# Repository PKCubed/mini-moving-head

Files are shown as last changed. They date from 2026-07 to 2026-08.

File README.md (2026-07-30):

# Mini Moving Head

This project aims to create a miniature moving head light fixture for my miniature stage. This fixture needs to have motorized pan and tilt, and should have a bright LED with a collimating lens to create as tight of a beam as possible. For now, a single color LED is acceptable due to the size constraints, as a multicolor LED with individual separate LED dies in side the package causes individual colored beams preventing color mixing.

This project consists of a custom circuit board with an RP2040 on board to take in unbalanced "DMX" signals from the "DMX" bus and read channel data for it's pan and tilt position and the brightness of it's LED. The circuit board drives two 9 gram servos with PWM to give pan and tilt and a constant current driver with PWM control for the LED. We'll need to make sure that the PWM is fast enough that it's not going to cause artifacts on cameras under any circumstances.



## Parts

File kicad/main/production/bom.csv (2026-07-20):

Designator | Footprint | Quantity | Value | LCSC Part #
C1, C2, C9 | C_0805 | 3 | 10uF | C15850
C10, C13 | C_0402 | 2 | 1uF | C52923
C11, C12, C3, C4, C5, C6 | C_0402 | 6 | 100nF | C1525
C15, C16 | C_0402 | 2 | 30pF | C1570
D2 | D_0603 | 1 | Red | C2286
D3 | D_0805 | 1 | Green | C2297
J1, J10, J7, J8 | 2-position | 4 | Conn_01x02
J2, J3 | 3-position | 2 | Conn_01x03
J4, J5 | PinHeader_1x02_P2.54mm_Vertical | 2 | Conn_01x02
J6 | TYPE-C-SMD_HX-TYPE-C-16PIN | 1 | Connector, USB-TYPE-C-16P | C2927039
L2 | IND-SMD_L3.5-W3.0 | 1 | 4.7uH
R1, R11 | R_0402 | 2 | 10kΩ | C25744
R10, R9 | R_1206 | 2 | 100mΩ | C25334
R2, R3 | R_0402 | 2 | 5.1kΩ | C25905
R4, R5 | R_0603 | 2 | 27Ω | C25190
R6 | R_0402 | 1 | 1kΩ | C11702
R7 | R_0402 | 1 | 510Ω | C25123
R8 | R_0603 | 1 | 430Ω | C23170
S1, S2 | SW_TS-1088-AR02016 | 2 | Tactile Button, 160gf | C720477
TP1 | TestPoint_Pad_D1.0mm | 1 | GPIO0
TP2 | TestPoint_Pad_D1.0mm | 1 | GPIO4
TP3 | TestPoint_Pad_D1.0mm | 1 | GPIO5
TP4 | TestPoint_Pad_D1.0mm | 1 | GPIO6
TP5 | TestPoint_Pad_D1.0mm | 1 | GPIO28
TP6 | TestPoint_Pad_D1.0mm | 1 | GPIO29
U2 | SOT-23-3_L2.9-W1.6-P1.90-LS2.8-BR | 1 | XC6206P332MR | C5446
U3 | SOIC-8_L5.3-W5.3-P1.27-LS8.0-BL | 1 | ~
U4 | SOT-23-5_L3.0-W1.7-P0.95-LS2.8-BR | 1 | ~
U5 | QFN-56-1EP_7x7mm_P0.4mm_EP3.2x3.2mm_ThermalVias | 1 | RP2040 | C2040
X1 | CRYSTAL-SMD_4P-L3.2-W2.5-BL | 1 | X322512MSB4SI | C9002

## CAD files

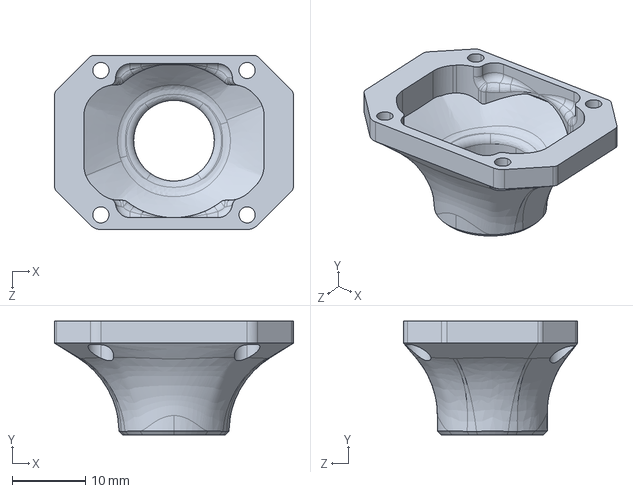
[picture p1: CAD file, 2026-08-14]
cad/Part7.STEP
32.6 x 15.5 x 23.8 mm

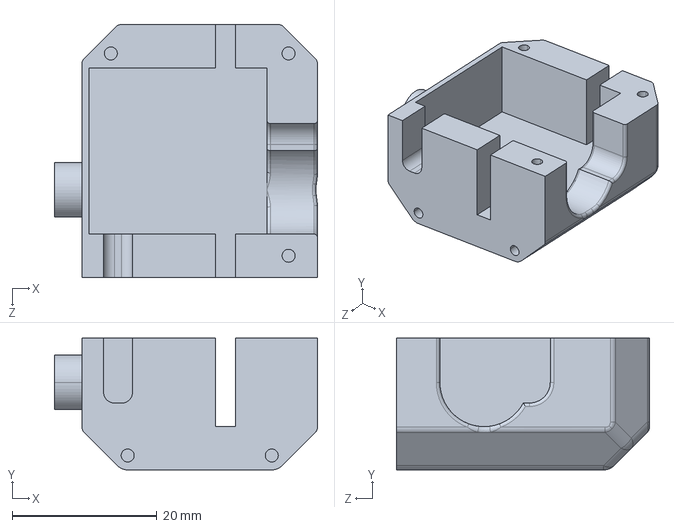
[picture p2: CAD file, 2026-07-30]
cad/Part4.STEP
36.4 x 18.2 x 35.0 mm

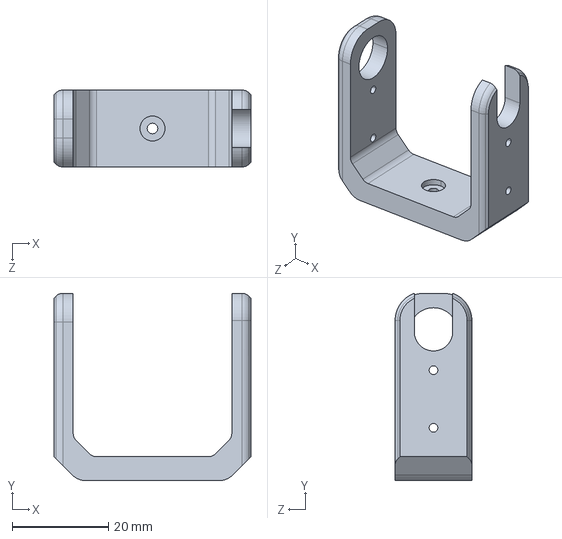
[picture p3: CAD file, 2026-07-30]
cad/Part2.STEP
41.0 x 39.0 x 16.0 mm

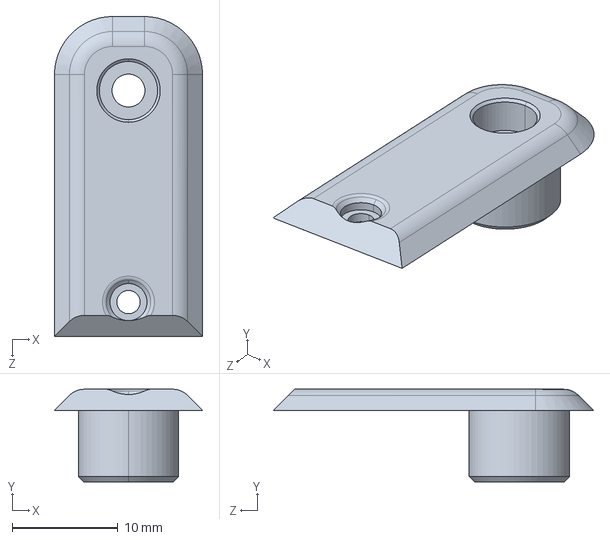
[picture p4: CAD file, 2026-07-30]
cad/Part3.STEP
14.0 x 8.75 x 30.2 mm

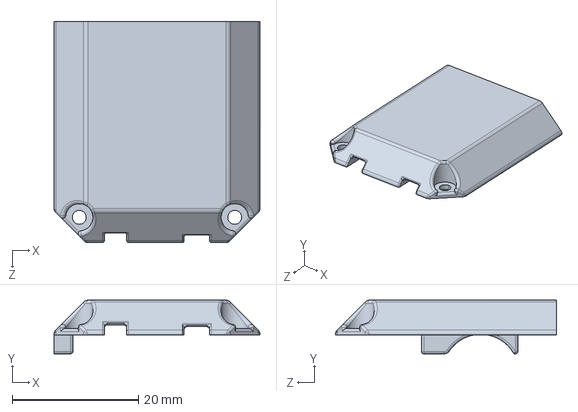
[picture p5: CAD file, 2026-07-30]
cad/Part5.STEP
32.6 x 8.50 x 35.0 mm

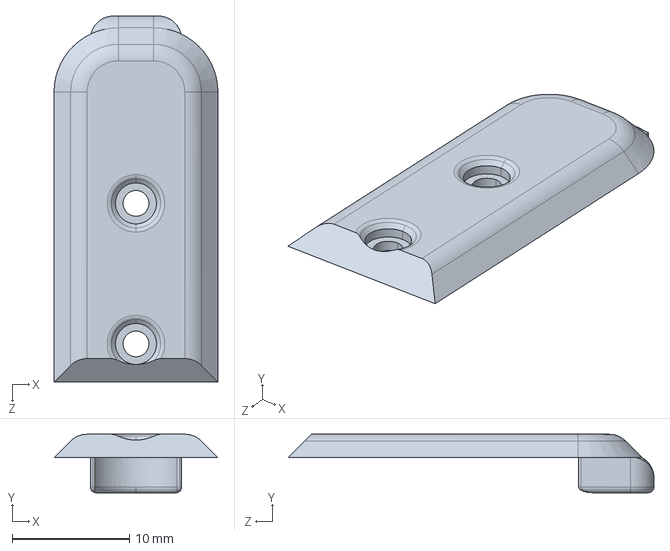
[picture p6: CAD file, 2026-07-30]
cad/Part6.STEP
14.0 x 5.00 x 31.2 mm

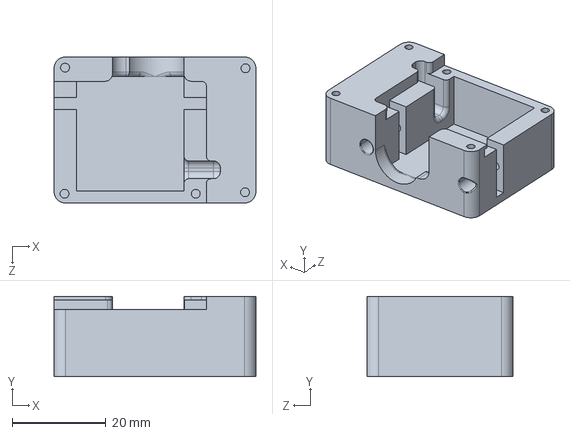
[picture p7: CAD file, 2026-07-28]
cad/Part1.STEP
43.1 x 17.1 x 31.2 mm

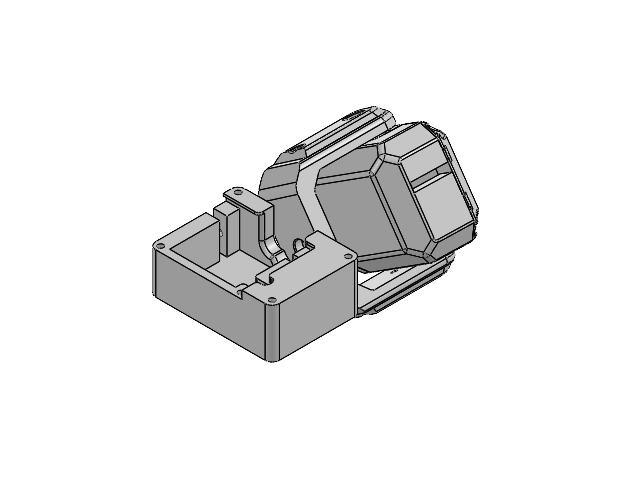
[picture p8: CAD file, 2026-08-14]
cad/Assem1.SLDASM


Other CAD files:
cad/Part1.3mf
cad/Part1.SLDPRT
cad/Part2.SLDPRT
cad/Part3.SLDPRT
cad/Part4.SLDPRT
cad/Part5.SLDPRT
cad/Part6.SLDPRT
cad/Part7.3MF
cad/Part7.SLDPRT

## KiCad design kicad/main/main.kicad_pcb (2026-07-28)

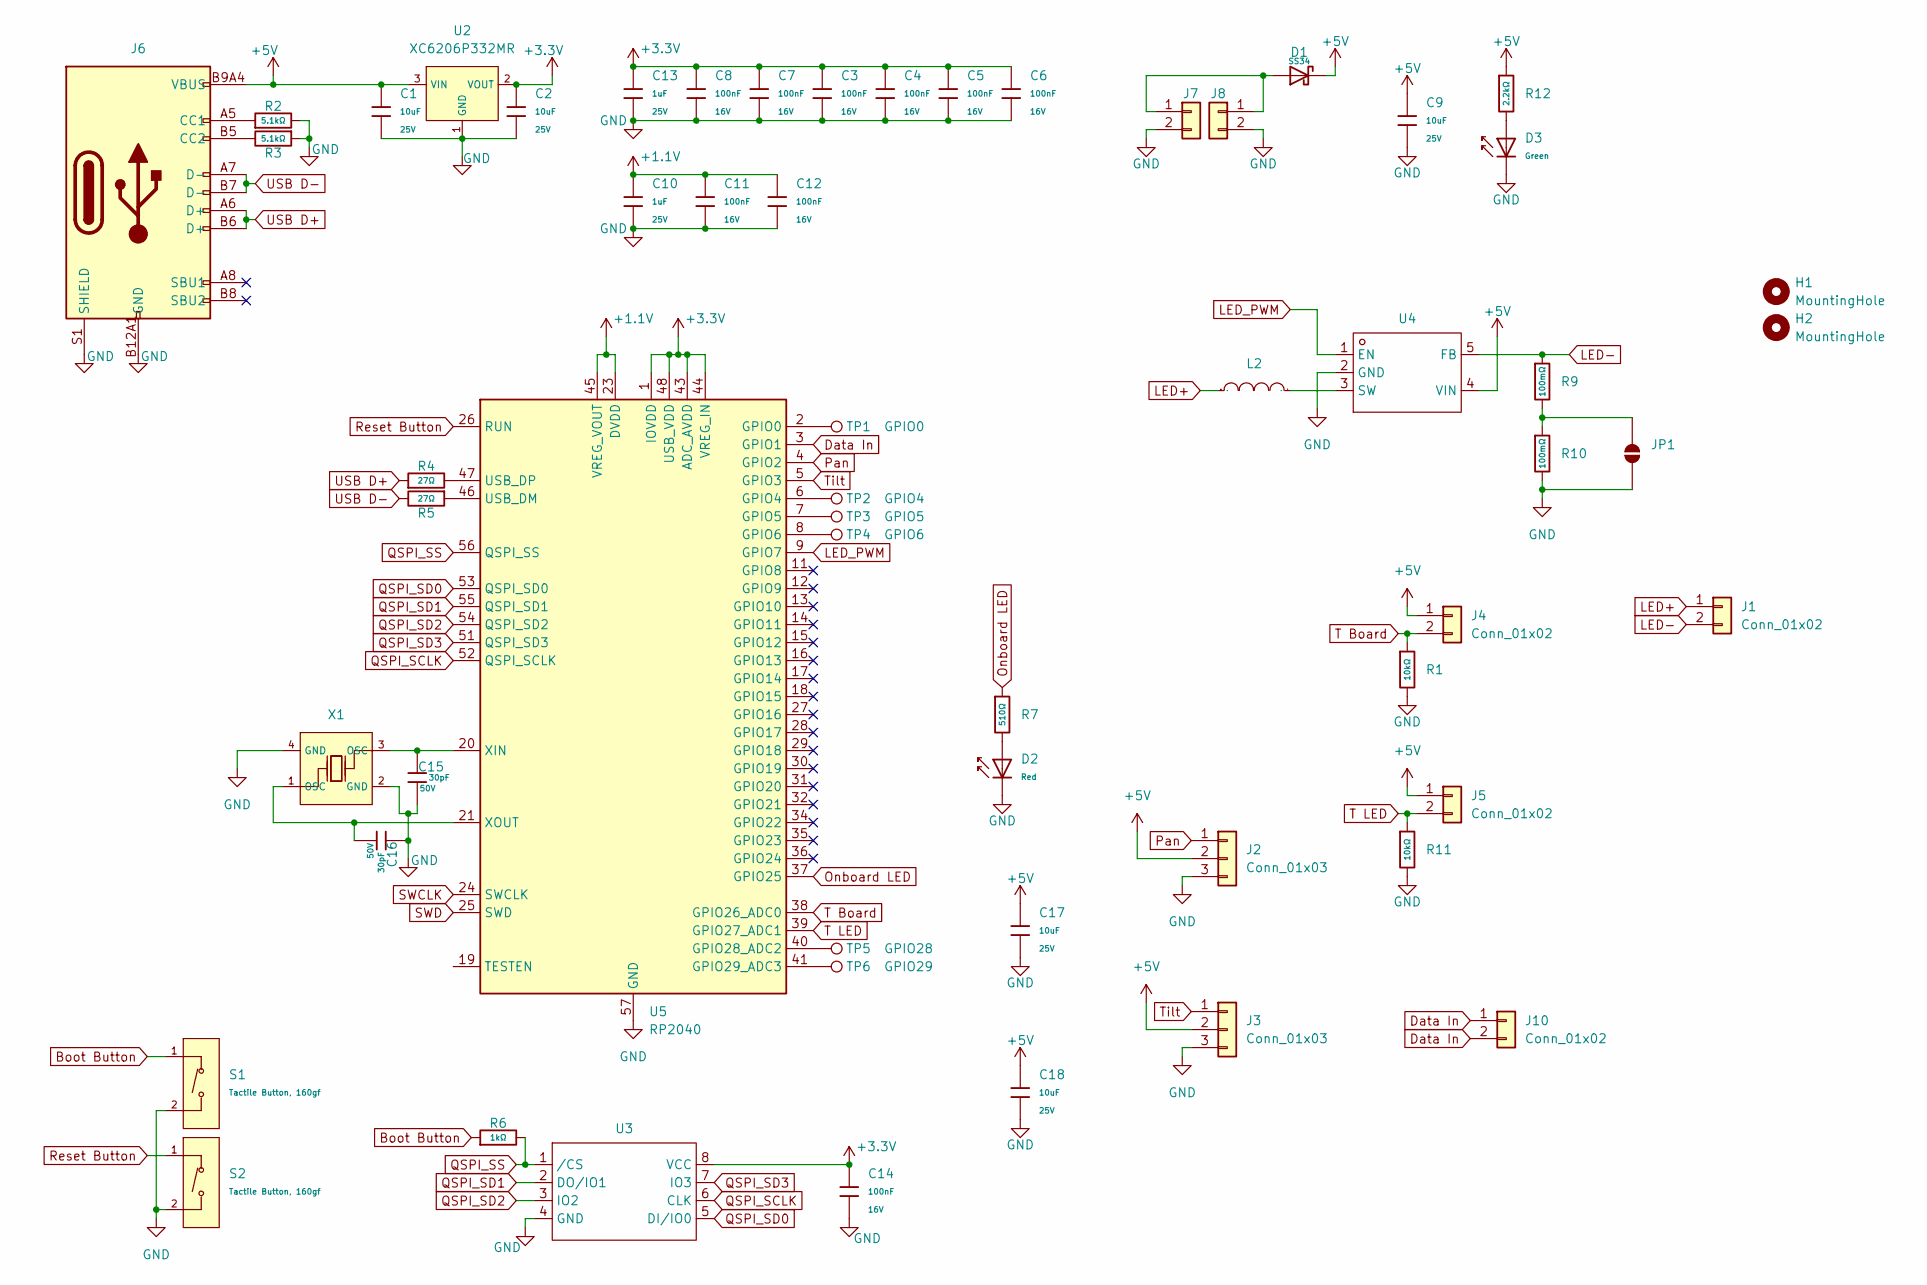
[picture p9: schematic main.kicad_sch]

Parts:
C1, C2, C9, C17, C18: 10uF; C_0805; Voltage Rated 25V; Tolerance ±10%; Part CL21A106KAYNNNE; LCSC C15850
C3, C4, C5, C6, C7, C8, C11, C12, C14: 100nF; C_0402; Voltage Rated 16V; Tolerance ±10%; Part CL05B104KO5NNNC; LCSC C1525
C10, C13: 1uF; C_0402; Voltage Rated 25V; Tolerance ±10%; Part CL05A105KA5NQNC; LCSC C52923
C15, C16: 30pF; C_0402; Voltage Rated 50V; Tolerance ±5%; Part 0402CG300J500NT; LCSC C1570
D1: SS34; D_SMA; Forward Voltage (Vf@If) 550mV@3A; Reverse Voltage (Vr) 40V; Part SS34; LCSC C8678
D2: Red; D_0603; Part KT-0603R; LCSC C2286
D3: Green; D_0805; Part KT-0805G; LCSC C2297
H1, H2: MountingHole; MountingHole_2.5mm
J1, J7, J8, J10: Conn_01x02; 2-position
J2, J3: Conn_01x03; 3-position
J4, J5: Conn_01x02; PinHeader_1x02_P2.54mm_Vertical
J6: Connector, USB-TYPE-C-16P; TYPE-C-SMD_HX-TYPE-C-16PIN; LCSC C2927039
JP1: SolderJumper_2_Open; SolderJumper-2_P1.3mm_Open_Pad1.0x1.5mm
L2: 4.7uH; IND-SMD_L3.5-W3.0; Manufacturer Part SM3521-4R7MT; LCSC Part Name 4.7uH ±20% 1.6A
R1, R11: 10kΩ; R_0402; Overload Voltage (Max) 50V; Tolerance ±1%; Part 0402WGF1002TCE; LCSC C25744
R2, R3: 5.1kΩ; R_0402; Overload Voltage (Max) 50V; Tolerance ±1%; Part 0402WGF5101TCE; LCSC C25905
R4, R5: 27Ω; R_0603; Overload Voltage (Max) 75V; Tolerance ±1%; Part 0603WAF270JT5E; LCSC C25190
R6: 1kΩ; R_0402; Overload Voltage (Max) 50V; Tolerance ±1%; Part 0402WGF1001TCE; LCSC C11702
R7: 510Ω; R_0402; Overload Voltage (Max) 50V; Tolerance ±1%; Part 0402WGF5100TCE; LCSC C25123
R9, R10: 100mΩ; R_1206; Overload Voltage (Max) 200V; Tolerance ±1%; Part 1206W4F100LT5E; LCSC C25334
R12: 2.2kΩ; R_0402; Overload Voltage (Max) 50V; Tolerance ±1%; Part 0402WGF2201TCE; LCSC C25879
S1, S2: Tactile Button, 160gf; SW_TS-1088-AR02016; Voltage Rating (Dc) 12V; Part TS-1088-AR02016; LCSC C720477
TP1: GPIO0; TestPoint_Pad_D1.0mm
TP2: GPIO4; TestPoint_Pad_D1.0mm
TP3: GPIO5; TestPoint_Pad_D1.0mm
TP4: GPIO6; TestPoint_Pad_D1.0mm
TP5: GPIO28; TestPoint_Pad_D1.0mm
TP6: GPIO29; TestPoint_Pad_D1.0mm
U2: XC6206P332MR; SOT-23-3_L2.9-W1.6-P1.90-LS2.8-BR; Output Voltage 3.3V; Dropout Voltage 680mV@(100mA); Part XC6206P332MR-G; LCSC C5446
U3: SOIC-8_L5.3-W5.3-P1.27-LS8.0-BL; Manufacturer Part W25Q16JVSSIQ; LCSC Part Name 支持双/四路SPI接口的3V、16Mbit 串行闪存
U4: SOT-23-5_L3.0-W1.7-P0.95-LS2.8-BR; Manufacturer Part PAM2804AAB010; LCSC Part Name 输出1A 降压型驱动
U5: RP2040; QFN-56-1EP_7x7mm_P0.4mm_EP3.2x3.2mm_ThermalVias; LCSC C2040
X1: X322512MSB4SI; CRYSTAL-SMD_4P-L3.2-W2.5-BL; Frequency Tolerance ±10ppm; Part X322512MSB4SI; LCSC C9002

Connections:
+1.1V: C10.1, C11.1, C12.1, U5.23 (DVDD), U5.45 (VREG_VOUT), U5.50 (DVDD)
+3.3V: C2.1, C3.1, C4.1, C5.1, C6.1, C7.1, C8.1, C13.1, C14.2, U2.2 (VOUT), U3.8 (VCC), U5.1 (IOVDD), U5.10 (IOVDD), U5.22 (IOVDD), U5.33 (IOVDD), U5.42 (IOVDD), U5.43 (ADC_AVDD), U5.44 (VREG_IN), U5.48 (USB_VDD), U5.49 (IOVDD)
+5V: C1.1, C9.1, C17.1, C18.1, D1.1, J2.2, J3.2, J4.1, J5.1, J6.A9B4 (VBUS), J6.B9A4 (VBUS), R12.1, U2.3 (VIN), U4.4 (VIN)
Boot Button: R6.1, S1.1 (A)
Data In: J10.1, J10.2, U5.3 (GPIO1)
GND: C1.2, C2.2, C3.2, C4.2, C5.2, C6.2, C7.2, C8.2, C9.2, C10.2, C11.2, C12.2, C13.2, C14.1, C15.2, C16.1, C17.2, C18.2, D2.1, D3.1, J2.3, J3.3, J6.A12B1 (GND), J6.B12A1 (GND), J6.S1 (SHIELD), J7.2, J8.2, JP1.1 (A), R1.2, R2.2, R3.1, R10.2, R11.2, S1.2 (B), S2.2 (B), U2.1 (GND), U3.4 (GND), U4.2 (GND), U5.57 (GND), X1.2 (GND), X1.4 (GND)
LED+: J1.1, L2.1
LED-: J1.2, R9.1, U4.5 (FB)
LED_PWM: U4.1 (EN), U5.9 (GPIO7)
unnamed: D2.2, R7.2
unnamed: D3.2, R12.2
unnamed: J6.A5 (CC1), R2.1
unnamed: J6.B5 (CC2), R3.2
unnamed: D1.2, J7.1, J8.1
unnamed: JP1.2 (B), R9.2, R10.1
unnamed: L2.2, U4.3 (SW)
unnamed: TP1.1 (1_1), U5.2 (GPIO0)
unnamed: TP2.1 (1_1), U5.6 (GPIO4)
unnamed: TP3.1 (1_1), U5.7 (GPIO5)
unnamed: TP4.1 (1_1), U5.8 (GPIO6)
unnamed: TP5.1 (1_1), U5.40 (GPIO28_ADC2)
unnamed: TP6.1 (1_1), U5.41 (GPIO29_ADC3)
unnamed: R5.1, U5.46 (USB_DM)
unnamed: R4.2, U5.47 (USB_DP)
unnamed: C15.1, U5.20 (XIN), X1.3 (OSC)
unnamed: C16.2, U5.21 (XOUT), X1.1 (OSC)
Onboard LED: R7.1, U5.37 (GPIO25)
Pan: J2.1, U5.4 (GPIO2)
QSPI_SCLK: U3.6 (CLK), U5.52 (QSPI_SCLK)
QSPI_SD0: U3.5 (DI/IO0), U5.53 (QSPI_SD0)
QSPI_SD1: U3.2 (DO/IO1), U5.55 (QSPI_SD1)
QSPI_SD2: U3.3 (IO2), U5.54 (QSPI_SD2)
QSPI_SD3: U3.7 (IO3), U5.51 (QSPI_SD3)
QSPI_SS: R6.2, U3.1 (/CS), U5.56 (QSPI_SS)
Reset Button: S2.1 (A), U5.26 (RUN)
SWCLK: U5.24 (SWCLK)
SWD: U5.25 (SWD)
T Board: J4.2, R1.1, U5.38 (GPIO26_ADC0)
T LED: J5.2, R11.1, U5.39 (GPIO27_ADC1)
Tilt: J3.1, U5.5 (GPIO3)
USB D+: J6.A6 (D+), J6.B6 (D+), R4.1
USB D-: J6.A7 (D-), J6.B7 (D-), R5.2

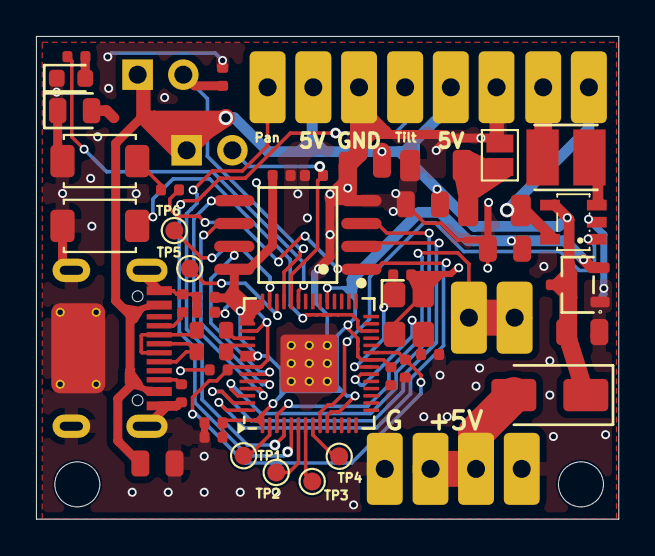
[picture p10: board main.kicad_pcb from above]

Board: 2 copper layers, 32.4 x 26.8 mm, 54 parts (0 on the bottom side), 39 nets.

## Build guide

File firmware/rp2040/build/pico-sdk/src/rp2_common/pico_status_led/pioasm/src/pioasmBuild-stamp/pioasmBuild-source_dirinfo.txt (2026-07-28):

# This is a generated file and its contents are an internal implementation detail.
# The download step will be re-executed if anything in this file changes.
# No other meaning or use of this file is supported.

method=source_dir
command=
source_dir=C:/dev/pico-sdk/tools/pioasm
work_dir=

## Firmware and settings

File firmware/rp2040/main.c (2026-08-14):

#include "pico/stdlib.h"
#include "hardware/pwm.h"
#include "hardware/uart.h"
#include "hardware/irq.h"
#include "bsp/board.h"
#include "tusb.h"
#include "msc_disk.h"

#include <math.h>

// Pin definitions
const uint LED_PIN = 25;
const uint SERVO_1_PIN = 2; // Pan (default)
const uint SERVO_2_PIN = 3; // Tilt (default)
const uint LED2_PIN = 7;    // High power LED
const uint DMX_RX_PIN = 1;  // DMX RX

// DMX State
volatile int dmx_channel = -1;
volatile uint8_t dmx_data[513];
volatile uint32_t last_dmx_time = 0;

void on_uart_rx() {
    while (uart_is_readable(uart0)) {
        // Read the Data Register and the Receive Status Register
        uint32_t dr = uart_get_hw(uart0)->dr;
        uint8_t data = dr & 0xFF;
        
        // Check for Framing Error (which indicates a BREAK condition in DMX)
        if (dr & UART_UARTDR_FE_BITS) {
            // Break detected, reset channel counter
            dmx_channel = 0;
            continue; // Skip processing this byte as data
        }

        if (dmx_channel >= 0 && dmx_channel <= 512) {
            dmx_data[dmx_channel] = data;
            if (dmx_channel > 0) {
                last_dmx_time = time_us_32();
            }
            dmx_channel++;
        }
    }
}

int main() {
    // Board init for TinyUSB
    board_init();
    tusb_init();
    msc_disk_init();

    // Setup LED PWM (GPIO 25)
    gpio_set_function(LED_PIN, GPIO_FUNC_PWM);
    uint led_slice = pwm_gpio_to_slice_num(LED_PIN);
    pwm_set_clkdiv(led_slice, 125.0f);
    pwm_set_wrap(led_slice, 1999);
    pwm_set_enabled(led_slice, true);

    // Setup LED2 PWM (GPIO 7)
    gpio_set_function(LED2_PIN, GPIO_FUNC_PWM);
    uint led2_slice = pwm_gpio_to_slice_num(LED2_PIN);
    pwm_set_clkdiv(led2_slice, 125.0f);
    pwm_set_wrap(led2_slice, 1999);
    pwm_set_enabled(led2_slice, true);

    // Setup Servo PWM (GPIO 2 and 3 share slice 1)
    gpio_set_function(SERVO_1_PIN, GPIO_FUNC_PWM);
    gpio_set_function(SERVO_2_PIN, GPIO_FUNC_PWM);
    uint servo_slice = pwm_gpio_to_slice_num(SERVO_1_PIN);

    pwm_config config = pwm_get_default_config();
    pwm_config_set_clkdiv(&config, 125.0f); // 1 MHz clock
    pwm_config_set_wrap(&config, 19999);    // 50 Hz
    pwm_init(servo_slice, &config, true);

    // DMX UART Setup
    uart_init(uart0, 250000);
    uart_set_format(uart0, 8, 2, UART_PARITY_NONE);
    gpio_set_function(DMX_RX_PIN, GPIO_FUNC_UART);
    
    // Disable UART FIFO to get accurate error flags per byte
    uart_set_fifo_enabled(uart0, false);
    
    // Set up UART IRQ
    irq_set_exclusive_handler(UART0_IRQ, on_uart_rx);
    irq_set_enabled(UART0_IRQ, true);
    uart_set_irq_enables(uart0, true, false);

    uint32_t last_led_toggle = 0;
    bool led_state = false;

    while (true) {
        // USB tasks
        tud_task();
        msc_disk_task();

        uint32_t now = time_us_32();
        
        // Status LED logic (blink slowly if DMX is active)
        bool dmx_active = (now - last_dmx_time < 1000000);
        if (dmx_active) { // 1 second timeout
            if (now - last_led_toggle > 500000) { // 1 Hz blink (500ms toggle)
                led_state = !led_state;
                pwm_set_gpio_level(LED_PIN, led_state ? 1999 : 0);
                last_led_toggle = now;
            }
        } else {
            pwm_set_gpio_level(LED_PIN, 0); // Off if no DMX
        }

        if (cfg_test_mode) {
            // Test mode: slow circle to test boundaries
            float t = (now / 1000000.0f) * 0.5f; // 0.5 radians per sec
            int16_t pan_offset = (int16_t)((cfg_pan_range / 2.0f) * sinf(t));
            int16_t tilt_offset = (int16_t)((cfg_tilt_range / 2.0f) * cosf(t));
            
            uint16_t pan_pwm = cfg_pan_center + pan_offset;
            uint16_t tilt_pwm = cfg_tilt_center + tilt_offset;
            
            // Slowly fade LED too
            uint32_t dim_pwm = (uint32_t)(999.0f + 999.0f * sinf(t * 2.0f));

            if (cfg_swap_pan_tilt) {
                pwm_set_gpio_level(SERVO_1_PIN, tilt_pwm);
                pwm_set_gpio_level(SERVO_2_PIN, pan_pwm);
            } else {
                pwm_set_gpio_level(SERVO_1_PIN, pan_pwm);
                pwm_set_gpio_level(SERVO_2_PIN, tilt_pwm);
            }
            
            pwm_set_gpio_level(LED2_PIN, dim_pwm);
        } else if (dmx_active && dmx_data[0] == 0) {
            uint16_t addr = cfg_dmx_start_address;
            if (addr >= 1 && addr <= 510) {
                uint8_t dmx_pan = dmx_data[addr];
                uint8_t dmx_tilt = dmx_data[addr + 1];
                uint8_t dmx_dim = dmx_data[addr + 2];

                // Calculate Pan/Tilt PWM values based on config
                // 0-255 maps to (center - range/2) to (center + range/2)
                int16_t pan_offset = ((dmx_pan - 127) * (int32_t)cfg_pan_range) / 255;
                int16_t tilt_offset = ((dmx_tilt - 127) * (int32_t)cfg_tilt_range) / 255;
                
                uint16_t pan_pwm = cfg_pan_center + pan_offset;
                uint16_t tilt_pwm = cfg_tilt_center + tilt_offset;
                
                // Dimmer mapping: 0-255 to 0-1999 with simple quadratic curve for better dimming
                uint32_t dim_pwm = (dmx_dim * dmx_dim * 1999) / (255 * 255);
                
                // Apply
                if (cfg_swap_pan_tilt) {
                    pwm_set_gpio_level(SERVO_1_PIN, tilt_pwm);
                    pwm_set_gpio_level(SERVO_2_PIN, pan_pwm);
                } else {
                    pwm_set_gpio_level(SERVO_1_PIN, pan_pwm);
                    pwm_set_gpio_level(SERVO_2_PIN, tilt_pwm);
                }
                
                pwm_set_gpio_level(LED2_PIN, dim_pwm);
            }
        } else if (!dmx_active) {
            // No DMX data: center servos and turn off LED
            if (cfg_swap_pan_tilt) {
                pwm_set_gpio_level(SERVO_1_PIN, cfg_tilt_center);
                pwm_set_gpio_level(SERVO_2_PIN, cfg_pan_center);
            } else {
                pwm_set_gpio_level(SERVO_1_PIN, cfg_pan_center);
                pwm_set_gpio_level(SERVO_2_PIN, cfg_tilt_center);
            }
            pwm_set_gpio_level(LED2_PIN, 0);
        }
    }
}

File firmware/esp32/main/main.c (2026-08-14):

#include <stdio.h>
#include <string.h>
#include "freertos/FreeRTOS.h"
#include "freertos/task.h"
#include "esp_netif.h"
#include "esp_eth.h"
#include "esp_event.h"
#include "esp_log.h"
#include "nvs_flash.h"
#include "driver/gpio.h"
#include "driver/uart.h"
#include "lwip/sockets.h"
#include "esp_mac.h"

static const char *TAG = "E131_DMX";

// -------------------------------------------------------------
// DMX Configuration
// -------------------------------------------------------------
#define DMX_UART_NUM      UART_NUM_1
#define DMX_TX_PIN        GPIO_NUM_4
#define DMX_RX_PIN        UART_PIN_NO_CHANGE
#define DMX_BAUD_RATE     250000
#define DMX_UNIVERSE      1
#define DMX_MAX_CHANNELS  512

// DMX packet is 513 bytes: Start Code (1 byte) + 512 channels
static uint8_t dmx_data[513] = {0};

void init_dmx_uart(void) {
    uart_config_t uart_config = {
        .baud_rate = DMX_BAUD_RATE,
        .data_bits = UART_DATA_8_BITS,
        .parity = UART_PARITY_DISABLE,
        .stop_bits = UART_STOP_BITS_2,
        .flow_ctrl = UART_HW_FLOWCTRL_DISABLE,
        .source_clk = UART_SCLK_DEFAULT,
    };
    ESP_ERROR_CHECK(uart_param_config(DMX_UART_NUM, &uart_config));
    ESP_ERROR_CHECK(uart_set_pin(DMX_UART_NUM, DMX_TX_PIN, DMX_RX_PIN, UART_PIN_NO_CHANGE, UART_PIN_NO_CHANGE));
    ESP_ERROR_CHECK(uart_driver_install(DMX_UART_NUM, 1024, 0, 0, NULL, 0));
}

void send_dmx_packet(void) {
    // A standard DMX break is at least 92us.
    // At 250k baud, 1 bit = 4us. So 92us = 23 bits. We use 25 bit times (~100us) to be safe.
    uart_write_bytes_with_break(DMX_UART_NUM, dmx_data, sizeof(dmx_data), 25);
}

// -------------------------------------------------------------
// E1.31 Parsing
// -------------------------------------------------------------
#define E131_PORT 5568

static void e131_task(void *pvParameters) {
    int sock = socket(AF_INET, SOCK_DGRAM, IPPROTO_IP);
    if (sock < 0) {
        ESP_LOGE(TAG, "Unable to create socket: errno %d", errno);
        vTaskDelete(NULL);
        return;
    }

    struct sockaddr_in server_addr;
    server_addr.sin_family = AF_INET;
    server_addr.sin_addr.s_addr = htonl(INADDR_ANY);
    server_addr.sin_port = htons(E131_PORT);

    if (bind(sock, (struct sockaddr *)&server_addr, sizeof(server_addr)) < 0) {
        ESP_LOGE(TAG, "Socket unable to bind: errno %d", errno);
        close(sock);
        vTaskDelete(NULL);
        return;
    }

    ESP_LOGI(TAG, "E1.31 UDP Server listening on port %d for Universe %d", E131_PORT, DMX_UNIVERSE);

    uint8_t rx_buffer[1024];
    while (1) {
        struct sockaddr_in source_addr;
        socklen_t socklen = sizeof(source_addr);
        int len = recvfrom(sock, rx_buffer, sizeof(rx_buffer), 0, (struct sockaddr *)&source_addr, &socklen);

        if (len < 0) {
            ESP_LOGE(TAG, "recvfrom failed: errno %d", errno);
            break;
        }

        // Basic E1.31 parsing
        if (len >= 126) {
            // Check ACN Packet Identifier
            if (memcmp(&rx_buffer[4], "ASC-E1.17\0\0\0", 12) == 0) {
                // Check root vector
                uint32_t root_vector = (rx_buffer[18] << 24) | (rx_buffer[19] << 16) | (rx_buffer[20] << 8) | rx_buffer[21];
                if (root_vector == 0x00000004) {
                    uint16_t universe = (rx_buffer[113] << 8) | rx_buffer[114];
                    if (universe == DMX_UNIVERSE) {
                        uint16_t property_value_count = (rx_buffer[123] << 8) | rx_buffer[124];
                        if (property_value_count > 0 && property_value_count <= 513) {
                            // Copy channel data. rx_buffer[125] is the start code.
                            memcpy(dmx_data, &rx_buffer[125], property_value_count);
                            send_dmx_packet();
                        }
                    }
                }
            }
        }
    }
    
    close(sock);
    vTaskDelete(NULL);
}

// -------------------------------------------------------------
// Ethernet Configuration for WT32-ETH01
// -------------------------------------------------------------
#define WT32_ETH01_MDC_PIN  23
#define WT32_ETH01_MDIO_PIN 18
#define WT32_ETH01_PHY_ADDR 1
#define WT32_ETH01_PHY_PWR  16

static void eth_event_handler(void *arg, esp_event_base_t event_base,
                              int32_t event_id, void *event_data) {
    uint8_t mac_addr[6] = {0};
    esp_eth_handle_t eth_handle = *(esp_eth_handle_t *)event_data;

    switch (event_id) {
    case ETHERNET_EVENT_CONNECTED:
        esp_eth_ioctl(eth_handle, ETH_CMD_G_MAC_ADDR, mac_addr);
        ESP_LOGI(TAG, "Ethernet Link Up");
        ESP_LOGI(TAG, "Ethernet HW Addr %02x:%02x:%02x:%02x:%02x:%02x",
                 mac_addr[0], mac_addr[1], mac_addr[2], mac_addr[3], mac_addr[4], mac_addr[5]);
        break;
    case ETHERNET_EVENT_DISCONNECTED:
        ESP_LOGI(TAG, "Ethernet Link Down");
        break;
    case ETHERNET_EVENT_START:
        ESP_LOGI(TAG, "Ethernet Started");
        break;
    case ETHERNET_EVENT_STOP:
        ESP_LOGI(TAG, "Ethernet Stopped");
        break;
    default:
        break;
    }
}

static void got_ip_event_handler(void *arg, esp_event_base_t event_base,
                                 int32_t event_id, void *event_data) {
    ip_event_got_ip_t *event = (ip_event_got_ip_t *)event_data;
    const esp_netif_ip_info_t *ip_info = &event->ip_info;

    ESP_LOGI(TAG, "Ethernet Got IP Address");
    ESP_LOGI(TAG, "~~~~~~~~~~~");
    ESP_LOGI(TAG, "ETHIP:" IPSTR, IP2STR(&ip_info->ip));
    ESP_LOGI(TAG, "ETHMASK:" IPSTR, IP2STR(&ip_info->netmask));
    ESP_LOGI(TAG, "ETHGW:" IPSTR, IP2STR(&ip_info->gw));
    ESP_LOGI(TAG, "~~~~~~~~~~~");
}
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

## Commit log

2026-06-22 Initial kicad files
    [IND-SMD_L6.0-W6.0_CR6045.step, SOT-89-5_L4.5-W2.5-H1.5-LS4.1-P1.50.step, main.kicad_pcb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]
2026-06-24 Started working on CC regulators
    [IND-SMD_L6.0-W6.0-H2.8.step, main.kicad_sch]
